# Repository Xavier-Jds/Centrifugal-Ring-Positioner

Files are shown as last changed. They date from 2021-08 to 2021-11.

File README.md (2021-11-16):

# Centrifugal Ring Positioner

The Centrifugal Ring Positioner (CRP) consists of a novel experimental setup for control engineering teaching. 
It has been developed through a master thesis project in the Department of Control Engineering and System Analysis of the Université libre de Bruxelles, Belgium (https://saas.ulb.ac.be/).
The CRP aims at illustrating several concepts of closed-loop control (system identification, model validation, PID control...) within a significant
multidisciplinary context. The setup is mainly composed by 3D-printed pieces. Hence, it is easy-to-build, easily reproducible and affordable.

The aim of this repository is to share this novel experimental setup and to provide all the required information and files to reproduce a CRP. 

The CRP is an unstable and nonlinear system, consisting of a ring able to slide on a rod thanks to the balance between gravity and centrifugal force. The control of the system aims at stabilizing the ring at any fixed position on the rod.

<p align="center">

A video of the CRP under PID cascade control can be found on the following link:
https://youtu.be/nnhnmA6dPzQ 

## Getting Started
This repository is divided in different folders:
* CAD: contains the Solidworks and STL files of the building pieces of the CRP
* Codes (Arduino & MATLAB): contains the Arduino and MATLAB files used to simulate and control the CRP
* Components: contains the datasheets of the components of the CRP
* Papers: contains the master thesis paper of the projet and the related published paper
* Teaching material: contains the teaching material related to the use of the CRP in our department.

## Components
* Microcontroller: Arduino DUE
* Motor: Maxon RE25 Precious Metal Brushes CLL 10W
* Motor driver: Escon 50/5 (+ 24V power supply)
* Ring position sensor: infrared Sharp GP2Y0A41SK0F
* Motor encoder:  Maxon HEDS 5540
* Slip ring: Senring H2056-0610
* Capacitors: 10 μF, 330 nF.
  
## Building pieces
Except the rod, all the pieces are 3D-printed. The CAD files can be found in the folder _CAD_.
 
## Softwares
The following softwares have been used for building and controlling the CRP. Alternatives can be used.
* Solidworks: CAD design of the building pieces
* MATLAB/Simulink: controllers design and simulation
* Arduino IDE: Arduino programming.

**All the construction plans and the software are released under license CC BY-NC-SA 4.0 (for the purpose of this license academic and training usage are to be considered non-commercial)**

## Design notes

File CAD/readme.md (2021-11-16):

**All the construction plans and the software are released under license CC BY-NC-SA 4.0 (for the purpose of this license academic and training usage are to be considered non-commercial)**

The CAD files of the Sharp infrared sensors and the Senring slip ring come from the following website:
  - Infrared sensor: https://grabcad.com/library/sharp-sensor-gp2y0a41sk0f-1 
  - Slip ring: https://www.senring.com/through-hole-slip-ring/small-hole/h2056.html

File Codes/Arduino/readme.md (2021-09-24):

This section contains several Arduino codes used for model identification and control of the CRP. 

  - *Control_CRP.ino*: cascade control of the CRP with PD or PID outerloop controller
  - *Control_velocity_CRP.ino*: control (proportional controller) of the angular velocity of the motor
  - *OpenLoop_step_motor_CRP.ino*: open loop step response of the motor (more information about the identification can be found in the papers).

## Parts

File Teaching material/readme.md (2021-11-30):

The CRP is currently used as a teaching experimental setup for the laboratory sessions of the Control System Design course at the Université libre de Bruxelles.
The aim of these labs is to design and implement a control strategy that meets one or several requirements for a real plant

The file *Control System Design Laboratory Material.pdf* consists of the laboratory statement.

The folder *Matlab codes* contains the different codes that are provided to the students for the labs:
  - *Identification*: code for the identification of a plant model by a black box experiment (uses *IdentifySystem()* and *Cost()* functions)
  - *Control sample*: example of a proportional controller for real-time control of a plant

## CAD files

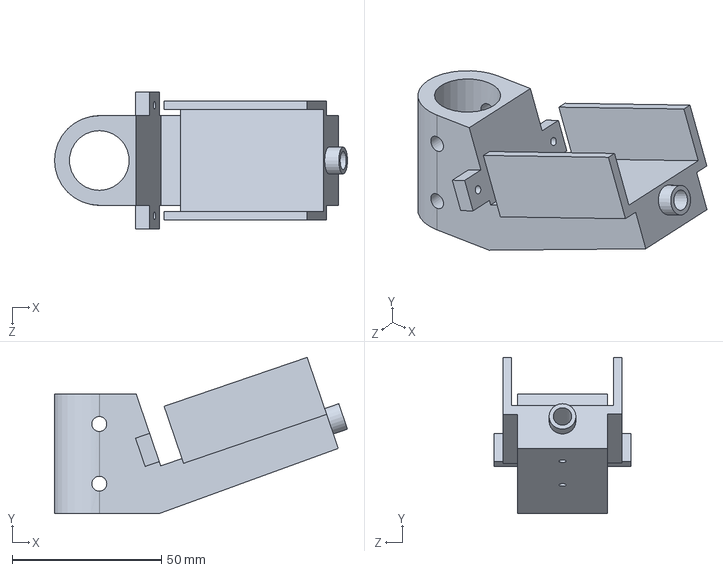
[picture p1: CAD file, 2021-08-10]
CAD/Rod_coupling.SLDPRT
98.1 x 52.3 x 46.0 mm

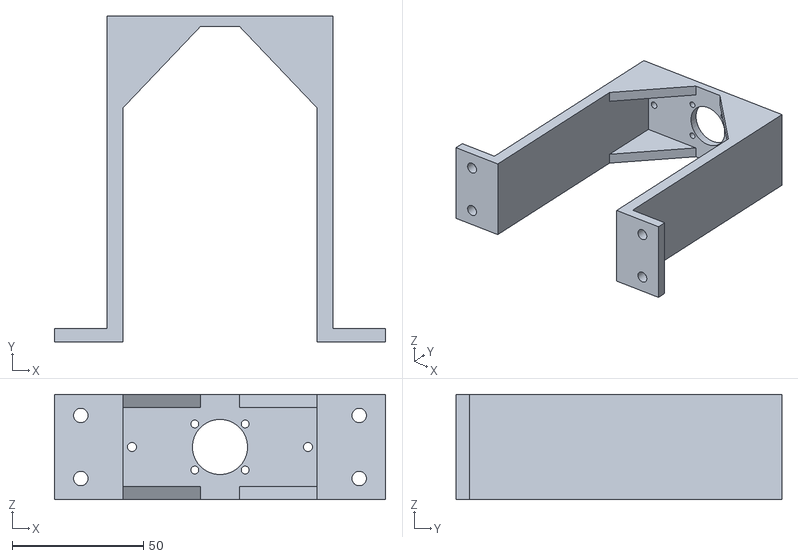
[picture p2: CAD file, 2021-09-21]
CAD/STL/Support_Motor.STL
126.0 x 124.0 x 40.0

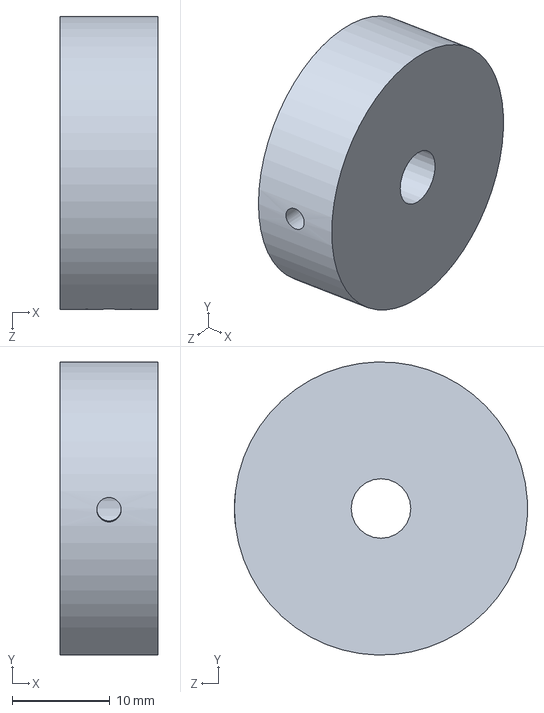
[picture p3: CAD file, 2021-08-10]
CAD/Stop_piece.SLDPRT
10.0 x 30.0 x 30.0 mm

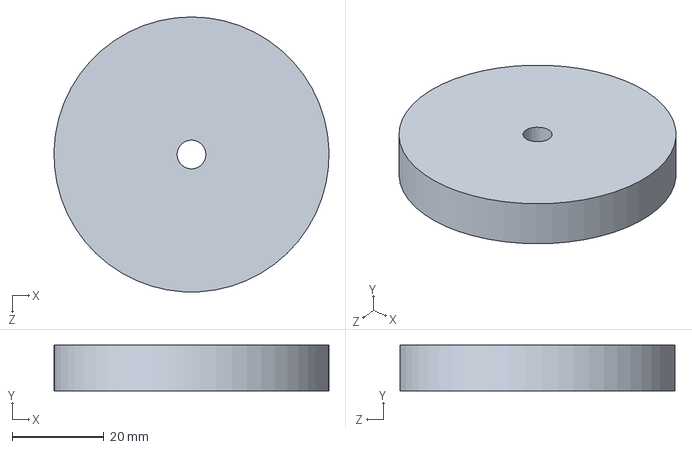
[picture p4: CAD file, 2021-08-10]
CAD/Ring.SLDPRT
60.0 x 10.0 x 60.0 mm

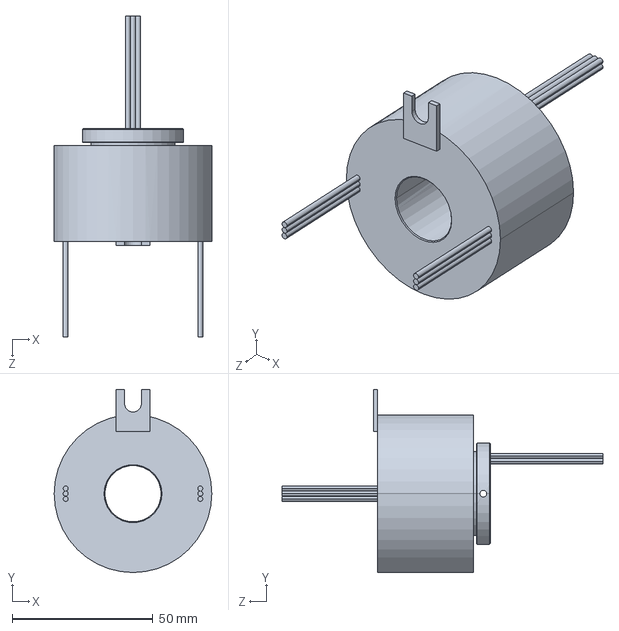
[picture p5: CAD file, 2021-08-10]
CAD/H2056-06.SLDPRT
56.0 x 65.0 x 114.0 mm

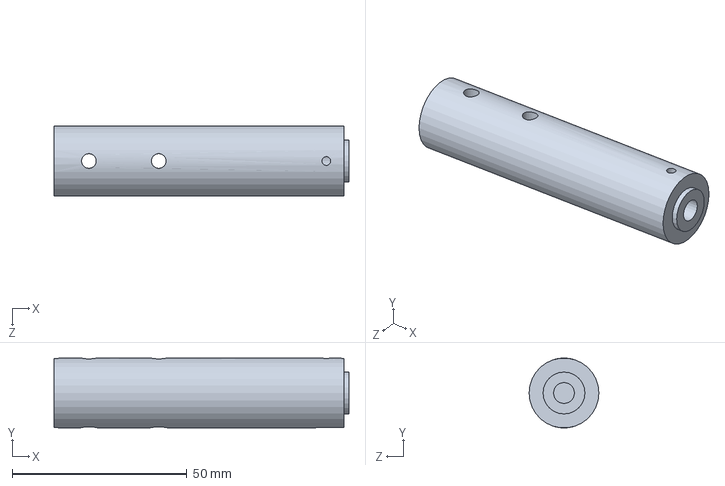
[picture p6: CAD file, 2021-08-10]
CAD/Motor_coupling.SLDPRT
84.5 x 20.0 x 20.0 mm

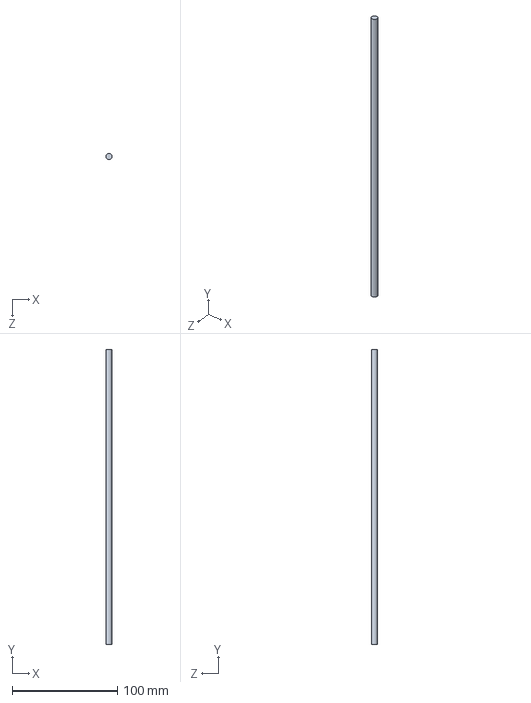
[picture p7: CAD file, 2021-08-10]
CAD/Rod.SLDPRT
6.00 x 280.0 x 6.00 mm

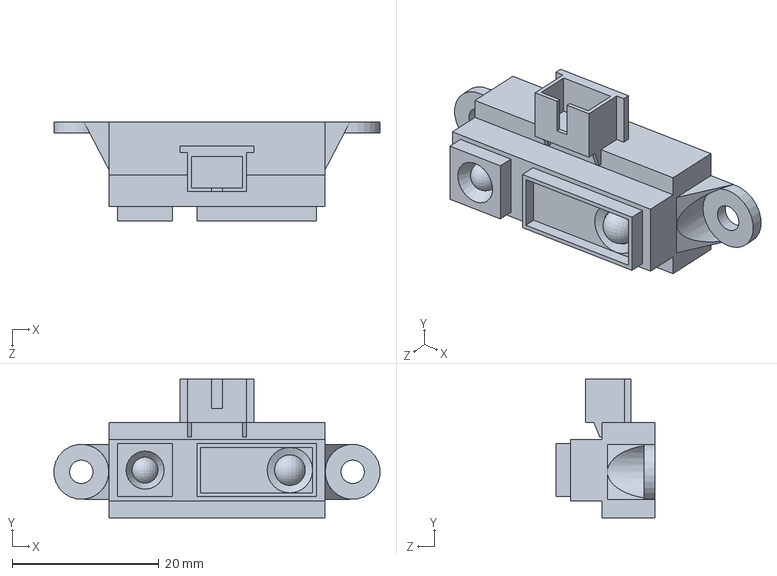
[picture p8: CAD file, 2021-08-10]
CAD/Long Range SHARP IR Sensors - #GP2Y0A21YK0F.SLDPRT
44.4 x 18.9 x 13.5 mm

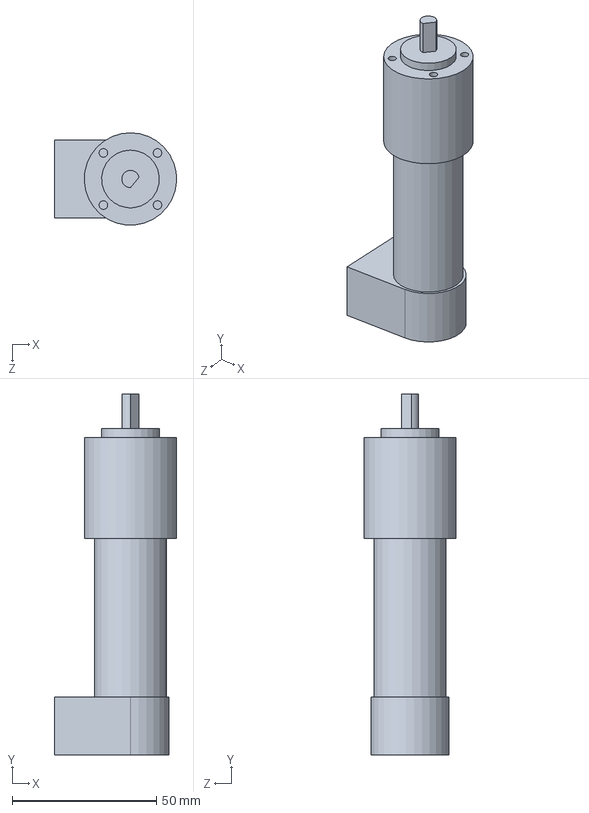
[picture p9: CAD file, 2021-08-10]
CAD/Gearmotor.SLDPRT
42.3 x 125.0 x 32.0 mm

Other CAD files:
CAD/Support_Moteur.SLDPRT
CAD/STL/Motor_coupling.STL
CAD/STL/Ring.STL
CAD/STL/Rod_coupling.STL
CAD/STL/Stop_piece.STL

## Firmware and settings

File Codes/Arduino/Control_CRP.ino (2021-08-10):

//Code for the cascade control of the centrifugal ring positioner

#include <Encoder.h>

Encoder myEnc(47, 37);          // definiton of the Arduino digital pins for the encoder
int sensorPin = A1;             // select the input pin for the position sensor


float current_time; 
float previous_time;
unsigned long time0;

float t_cycle = 1000;           // sampling period (in microsecondqs ; 1000 = 1ms)  
int t_exp = 20000000;           // duration of the ring control experiment (in microseconds)
int nb_cycles = t_exp / t_cycle; 
int t_start = 30000000;         // start time of the ring position control
int t_end = 50000000;           // end time of the ring position control
int t_mot = 10000000;           // start time of the system rotation

// Saving of the data in lists
float cmd_sav[3000];            // saving list of commands data
float time_sav[3000];           // saving list of time data
float vel_sav[3000];            // saving list of system angular velocity data
float pos_sav[3000];            // saving list of ring position data
float sp_sav[3000];             // saving list of ring setpoint data
float reg_sav[3000];            // saving list of outer controller data

float vel;                      // angular velocity of the system
float newTime;                  // involved in velocity calculation
float oldTime = 0;              // involved in velocity calculation
long oldPosition  = 0;          // involved in velocity calculation

float kp = 0.15;                // inner loop P controller gain
float cmd = 0;                  // output of the inner loop P controller
float cmd_I;                    // output of the inner loop P controller (in A)
float sp_vel = 0;               // setpoint of the system angular velocity (in rad/s)
float sp_pos = 0.08;            // setpoint of the ring position (in m) 
float err_pos_prev = 0;         // previous ring position error 
float err_pos_prevprev;         // second previous ring position error
float reg_out_prev = 0;         // previous outer loop controller output                                         
float reg_out_prevprev;         // second previous outer loop controller output
float reg_out;                  // outer loop controller output
float sp_pos_prec;              // previous ring position setpoint
float reg;                      // outer loop controller output (+ equilibrium point)
float w0;                       // equilibrium point velocity
float ring_position;            // position of the ring
float sensorValue;              // variable to store the value coming from the sensor

int k;


//Uncomment for the PID outer loop controller 
     
float num1 =  1000*1.051456138860390;
float num2 = 1000*2.080401718559944;
float num3 = 1000*1.029045015404039;
float den1 = 1.000000000000000; 
float den2 = 1.926343922603877;
float den3 = 0.926343922603876;

//Uncomment for the PD outer loop controller
/*
float num1 =  1000*1.591681613228143;
float num2 = 1000*1.567522419842214;
float den1 = 1.000000000000000; 
float den2 = 0.926343922603876;
*/

// List with the data from the position sensor characteristic
float list_bit[14] = {2556, 2383, 2046, 1789, 1567, 1432, 1331, 1214, 1137, 1070, 994, 931, 893, 878};
float list_abs[14] = {0.1845, 0.1557, 0.1347, 0.1187, 0.1061, 0.09596, 0.08756, 0.08051, 0.074515, 0.06934, 0.06485, 0.0609, 0.0574, 0.05549};


void setup() {
  Serial.begin(9600);
  analogWriteResolution(12);
  analogReadResolution(12);
  Serial.println("Waiting phase... ");
}

void loop() {
  while (micros() < t_mot) {                                               // waiting phase of duration t_mot to enable the motor with the switch
    analogWrite(DAC0, 2048);
  }

  while (micros() >= t_mot and micros() < t_start) {                       // start of the system rotation at time t_mot, inner loop control
    Serial.println("Start of the experiment... ");
    Serial.println("System rotation... ");
    time0 = micros();
    previous_time = time0;


    for (int j = 0; j < nb_cycles; j = j + 1) {
      current_time = micros();
      long newPosition = myEnc.read();                                     // reading of the motor angular position via the encoder
      vel = ((newPosition - oldPosition) / (t_cycle)) * 6.28 * 100 / 7;    // system angular velocity calculation
      oldPosition = newPosition;

      if (micros() >= t_mot and micros () < t_mot + 10000000) {            // linear increase of the system velocity from rest to equilibrium point velocity
        sp_vel = sp_vel + 0.0006893; 
      }
      if (micros() >= t_mot + 10000000 and micros() < t_mot + 20000000 ) { // constant system velocity at equilibrium point velocity
        sp_vel = sp_vel;
      }

      float error_vel = sp_vel - vel;                                      // system angular velocity error
      cmd_I = kp*error_vel;                                                // inner loop P controller command
      cmd = int((cmd_I+0.652)*4095/(2*0.652));                             // conversion of the inner loop command into Arduino output voltage
      
      if (cmd < 0){                                                        // normalization of the P controller command
        cmd = 0;                                               
      }
      else if (cmd > 4095){
        cmd = 4095;
      }
      analogWrite(DAC0, cmd);                                               // command signal sent to the motor driver

      previous_time = current_time;
      while (micros() - time0 < (j + 1)*t_cycle) { 
      }
    }

    w0 = sp_vel;                                                            // definition of the system angular equilibrium velocity as the current system velocity
    sp_pos = bit2m(analogRead(sensorPin));                                  // definition of the first ring position setpoint as the current sensor measure
    err_pos_prev =  0 ;
    err_pos_prevprev =  0 ;
    reg_out_prev =0; 
    reg_out_prevprev = 0; 
    
  } 

  while (micros() >= t_start and micros() < t_end) {                        // start of the cascade control of the system
    Serial.println("Start of the ring position control... ");
    time0 = micros();
    previous_time = time0;


    for (int j = 0; j < nb_cycles; j = j + 1) {                             // definition of the ring position setpoint profile
      current_time = micros();

      if (micros() >= t_start and micros () < t_start + 5000000) {
        sp_pos = sp_pos + 0.000016;
      }
      if (micros() >= t_start + 5000000 and micros() < t_start + 10000000 ) {
        sp_pos = sp_pos;
      }
      if (micros() >= t_start + 10000000 and micros() < t_start + 15000000 ) {
        sp_pos = sp_pos-0.000008;
      }
      if (micros() >= t_start + 15000000 and micros() < t_start + 20000000 ) {
        sp_pos = sp_pos;
      }


      long newPosition = myEnc.read();                                       // reading of the motor angular position via the encoder
      vel = ((newPosition - oldPosition) / (t_cycle)) * 6.28 * 100 / 7;      // system angular velocity calculation
      oldPosition = newPosition; 
      
      ring_position = analogRead(sensorPin);                                 // reading of the position sensor signal 
      sensorValue = bit2m(ring_position);                                    // conversion of the sensor signal into a position via the defined function bit2m
      float error_ring_pos = sp_pos - sensorValue;                           // ring position error

      // uncomment for PID outer loop controller
      reg_out = (den2 * reg_out_prev - den3 * reg_out_prevprev + num1 * error_ring_pos - num2 * err_pos_prev + num3 * err_pos_prevprev); 

      // uncomment for PD outer loop controller
      //reg_out = (den2* reg_out_prev + num1 * error_ring_pos - num2 * err_pos_prev); 
      
      reg = reg_out + w0;                                                    // addition of the equilibrium velocity to the discrete controller output 
      float error_vel = (reg - vel);                                         // system angular velocity error                                   
      cmd_I = kp*error_vel;                                                  // inner loop P controller command
      cmd = int((cmd_I+0.652)*4095/(2*0.652));                               // conversion of the inner loop command into Arduino output voltage
      
     
      err_pos_prevprev = err_pos_prev;
      err_pos_prev = error_ring_pos;
      reg_out_prevprev = reg_out_prev;
      reg_out_prev = reg_out;
      sp_pos_prec = sp_pos;
      
      if (cmd < 0){                                                          // normalization of the P controller command
        cmd = 0;                                               
      }
      else if (cmd > 4095){
        cmd = 4095;
      }
      analogWrite(DAC0, cmd);                                                // command signal sent to the motor driver

      

      if (j % 10 == 0) {                                                     // saving of the data in lists every 10ms
        k = j/10;
        reg_sav[k] = reg;
        sp_sav[k] = sp_pos;
        pos_sav[k] = sensorValue;
        cmd_sav[k] = int(cmd);         
        time_sav[k] = (current_time - t_start) / 1000000.0; 
        vel_sav[k] = vel;   
      }
   
      previous_time = current_time;
      
      while (micros() - time0 < (j + 1)*t_cycle) { 
      }
    }

    analogWrite(DAC0, 2048);  
    Serial.println("Display of the saved data... ");
    for (int j = 0; j < nb_cycles/10; j = j + 1) {
      Serial.print(vel_sav[j], 3);
      Serial.print(", \t");
      Serial.print(cmd_sav[j]);
      Serial.print(", \t");
      Serial.print(reg_sav[j],2);
      Serial.print(", \t");
      Serial.print(sp_sav[j],4);
      Serial.print(", \t");
      Serial.print(pos_sav[j], 4);
      Serial.print(", \t");
      Serial.println(time_sav[j], 3);
    }

  }
}


// Function convertting a sensor signal into a ring position
// Input: sensor signal in bit
// Output: ring position in m
float bit2m(float pos_bit) {  
  float val = 0;

  if (pos_bit > 2556){
          val = 0.08;
      }
  if ((pos_bit < 2556) && (pos_bit >= 2383)){
          val = ((1/(((0.1845-0.1557)*(pos_bit-2383))/(2556-2383)+0.1557))-0.42)/100.0 + 0.03;
      }
  if ((pos_bit < 2383) && (pos_bit >= 2046)){
          val = ((1/(((0.1557-0.1347)*(pos_bit-2046))/(2383-2046)+0.1347))-0.42)/100.0 + 0.03;
      }
   if ((pos_bit < 2046) && (pos_bit >= 1789)){
          val = ((1/(((0.1347-0.1187)*(pos_bit-1789))/(2046-1789)+0.1187))-0.42)/100.0 + 0.03;
      }
   if ((pos_bit < 1789) && (pos_bit >= 1567)){
          val = ((1/(((0.1187-0.1061)*(pos_bit-1567))/(1789-1567)+0.1061))-0.42)/100.0 + 0.03;
      }
   if ((pos_bit < 1567) && (pos_bit >= 1432)){
          val = ((1/(((0.1061-0.09596)*(pos_bit-1432))/(1567-1432)+0.09596))-0.42)/100.0 + 0.03;
      }
   if ((pos_bit < 1432) && (pos_bit >= 1331)){
          val = ((1/(((0.09596-0.08756)*(pos_bit-1331))/(1432-1331)+0.08756))-0.42)/100.0 + 0.03;
      }
   if ((pos_bit < 1331) && (pos_bit >= 1214)){
          val = ((1/(((0.08756-0.08051)*(pos_bit-1214))/(1331-1214)+0.08051))-0.42)/100.0 + 0.03;
      }
   if ((pos_bit < 1214) && (pos_bit >= 1137)){
          val = ((1/(((0.08051-0.074515)*(pos_bit-1137))/(1214-1137)+0.074515))-0.42)/100.0 + 0.03;
      }
   if ((pos_bit < 1137) && (pos_bit >= 1070)){
          val = ((1/(((0.074515-0.06934)*(pos_bit-1070))/(1137-1070)+0.06934))-0.42)/100.0 + 0.03;
      }
   if ((pos_bit < 1070) && (pos_bit >= 994)){
          val = ((1/(((0.06934-0.06485)*(pos_bit-994))/(1070-994)+0.06485))-0.42)/100.0 + 0.03;
      }
   if ((pos_bit < 994) && (pos_bit >= 931)){
          val = ((1/(((0.06485-0.0609)*(pos_bit-931))/(994-931)+0.0609))-0.42)/100.0 + 0.03;
      }
   if ((pos_bit < 931) && (pos_bit >= 893)){
          val = ((1/(((0.0609-0.0574)*(pos_bit-893))/(931-893)+0.0574))-0.42)/100.0 + 0.03;
      }
   if ((pos_bit < 893) && (pos_bit >= 878)){
          val = ((1/(((0.0574-0.05549)*(pos_bit-878))/(893-878)+0.05549))-0.42)/100.0 + 0.03;
      }
   if (pos_bit < 878){
          val = 0.206;
      }
       
    return val;    
        
}



    

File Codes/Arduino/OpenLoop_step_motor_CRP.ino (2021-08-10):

// code for the open loop step response of the motor 


#include <Encoder.h>

Encoder myEnc(47, 37);                                    // definiton of the Arduino digital pins for the encoder
float current_time;
float previous_time;
unsigned long time0;

float t_cycle=10000;                                      // sampling period (in microsecondqs ; 1000 = 1ms)
int t_test = 40000000;   
int nb_cycles = t_test/t_cycle;                            // duration of the motor control experiment (in microseconds)
int t_start = 10000000;                                   // start time of the experiement
int t_end = t_start + t_test;                             // end time of the experiment
int t_step = t_start + 20000000;                          // time of the step change in the motor current

// Saving of the data in lists
float cmd_sav[4000];                                      // saving list of commands data
float time_sav[4000];                                     // saving list of time data
float vel_sav[4000];                                      // saving list of system angular velocity data
unsigned long t_cycle_sav[4000];    


float vel;                                                // angular velocity of the system
float newTime;                                            // involved in velocity calculation
float oldTime = 0;                                        // involved in velocity calculation
long oldPosition  = 0;                                    // involved in velocity calculation

float cmd1 = 2114;                                        // motor command before the step
float cmd2 = 2130;                                        // motor command after the step
float cmd;                                                // actual motor command


void setup(){
  Serial.begin(9600);
  analogWriteResolution(12);
  Serial.println("Waiting phase... ");
}

void loop(){
  while (micros()<t_start){                              // waiting phase of duration t_start to enable the motor with the switch
    analogWrite(DAC0, 2048);
  }
  
  while (micros()>=t_start and micros()<t_end){          // start of the experiment
  Serial.println("Start of the experiment... ");
  time0 = micros();
  previous_time=time0;


  for (int j = 0; j < nb_cycles; j = j + 1) {    
    current_time = micros();  
    if (micros()<t_step){
      cmd = cmd1;
    }
    else {
      cmd = cmd2;
    }
    long newPosition = myEnc.read();                     // reading of the motor angular position via the encoder
    if (newPosition < oldPosition){                     
      newPosition = 0;
    }
    vel = ((newPosition - oldPosition) / (t_cycle)) * 6.28 * 100 / 7;          // system angular velocity calculation
    oldPosition = newPosition;
    
  
    analogWrite(DAC0, cmd);
  
    // saving of the data in lists every 10ms
    cmd_sav[j] = cmd;       
    time_sav[j]=(current_time-t_start)/1000000.0;     
    vel_sav[j]=vel;
    previous_time =current_time;  
    
    previous_time=current_time;  
    while(micros()-time0 < (j+1)*t_cycle){   
      }
  }
  
    analogWrite(DAC0, 2048);  
    Serial.println("Display of the saved data... ");
    for (int j = 0; j < nb_cycles/10; j = j + 1) {
      Serial.print(vel_sav[j],3);
      Serial.print(", \t");
      Serial.print(cmd_sav[j]);
      Serial.print(", \t");
      Serial.println(time_sav[j],3);
}

}

}

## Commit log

2021-08-10 Create cad
2021-08-10 Update cad
2021-09-21 Create stl
2021-09-21 Update and rename cad to readme
